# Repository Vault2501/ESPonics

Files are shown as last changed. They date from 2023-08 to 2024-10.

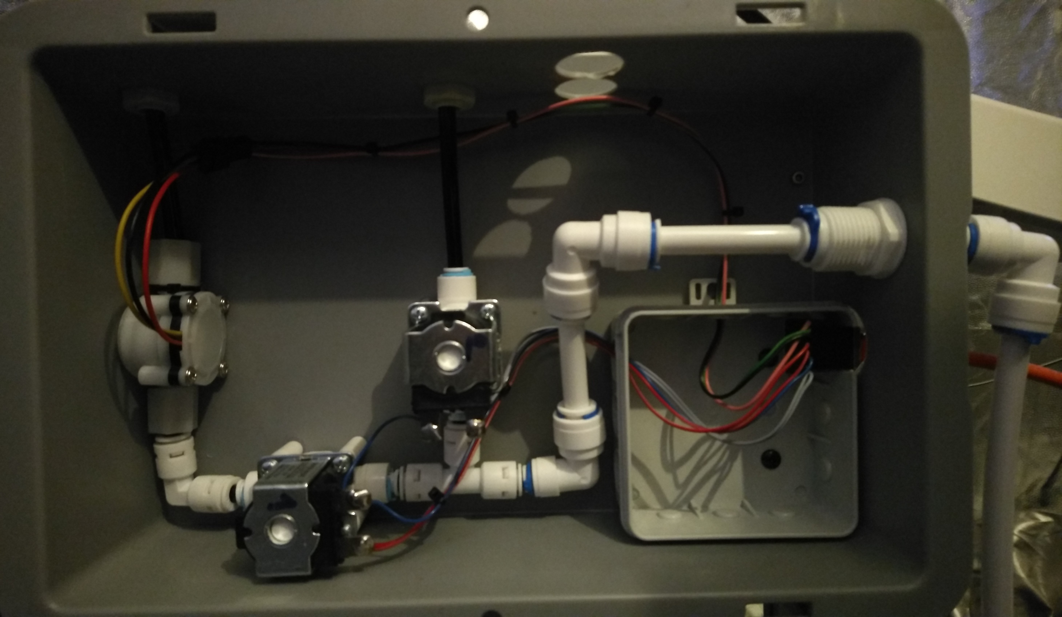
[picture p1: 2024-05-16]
media/20240514_195604_001.jpg

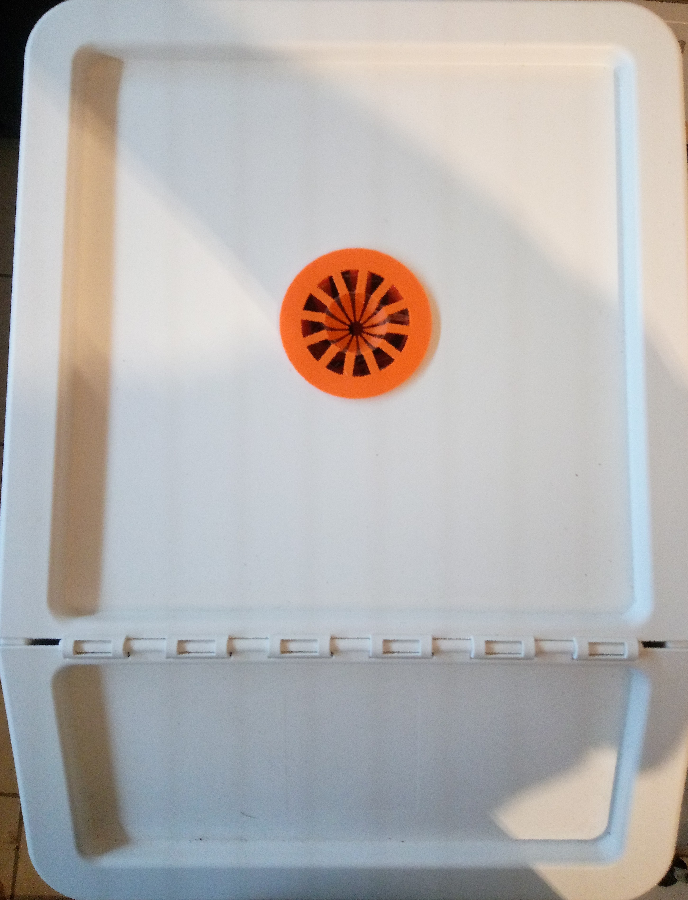
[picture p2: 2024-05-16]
media/IMG_20240429_215926_520.jpg

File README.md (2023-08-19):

# ESPonics
ESPonics is a ESP32 based automated Aeroponics system. It consists of fan, light and pump control as well as sensors for temperature, humidity, water level, ph and ec and is controlled via a web interface.

# Status
This is still WIP

Done:
* Pump control
* Fan Control
* Light Control
* Test Web UI

Current WIP:
* Sensors
* Case models

Todo:
* Userfriendly UI
* Parameter configuration
* Automatic control
* PCB

# Documentation
Documentation will go to the documentaiton folder

# Media
Photos and Videos of this project can be found here:
* Grow and feeding container with pumps: https://pixel.tchncs.de/i/web/post/594626511061922875
* WIP main controller,sensor and light/fan modules: https://pixel.tchncs.de/i/web/post/594629490395300993
* Finished prototype modules: https://pixel.tchncs.de/i/web/post/597583425622062798
* Video testing the pumps: https://makertube.net/w/gAhuFigTPs9yXAJNz8wZ4G

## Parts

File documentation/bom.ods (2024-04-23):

ID
 | Root and Water Container
 | Part | Amount | Source | Price | Comment
2 | IKEA SORTERA 37L | 2 | https://www.ikea.com/de/de/p/sortera-abfalleimer-mit-deckel-weiss-10255897/ | 14.99€
3 | Injectors and hose | 1 | https://www.amazon.de/Yosoo-Drip-Bew%C3%A4sserungskit-K%C3%BChlsystem-Schlauch-Sprinkter-Garten-Terrasse/dp/B072VDN3VG (https://www.amazon.de/Yosoo-Drip-Bewässerungskit-Kühlsystem-Schlauch-Sprinkter-Garten-Terrasse/dp/B072VDN3VG) | 5.26
14 | Plant basket | 1
 | Controller and Modules
 | Part | Amount | Source | Price | Comment
 | Pumps and Valves
 | Part | Amount | Source | Price | Comment
5 | 12V diaphragm pump | 2 | https://www.amazon.de/-/en/gp/product/B01MTNBHPT | 25.99 | Needs adapter for quick connect piping, find better one
1 | Pipe and connectors | 1 | https://www.amazon.de/-/en/gp/product/B099J9TKBH | 15.99
4 | Flow sensor | 1 | https://www.amazon.de/DollaTek-Wasserdurchfluss-Schalter-Durchflussmesser-Z%C3%A4hler-Wei%C3%9F/dp/B07DJ55PPX | 7.99
6 | Solenoid valve | 2 | https://www.amazon.de/Wasserventil-Kunststoff-Elektromagnetventil-Schnellkupplung-Normalerweise/dp/B07Q8KP71J/ | 10.99
 | Light and Fans
 | Part | Amount | Source | Price | Comment
12 | Climate fan | 1
13 | Water cooling fan | 1
15 | LED Light | 1
 | Sensors
 | Part | Amount | Source | Price | Comment
11 | Humidty/Temp | 1 | https://www.amazon.de/-/en/gp/product/B00L3I91TO | 9.49
7 | Temperature | 1 | https://amazon.de/AZDelivery-digitaler-Temperatursensor-Temperaturfühler-wasserdicht/dp/B01MZG48OE | 6.99
8 | TDS | 1 | https://amazon.de/CQRobot-Ocean-Compatible-Scientific-Laboratory/dp/B08KXRHK7H | 11.99
9 | Level | 1 | https://www.amazon.de/Ber%C3%BChrungsloser-Fl%C3%BCssigkeitsstandsensor-Kapazitiver-Wasserstandsschalter-Fl%C3%BCssigkeitserkennungssensor/dp/B0C1BKQ6FH/ (https://www.amazon.de/Berührungsloser-Flüssigkeitsstandsensor-Kapazitiver-Wasserstandsschalter-Flüssigkeitserkennungssensor/dp/B0C1BKQ6FH/) | 6.99
10 | pH | 1 | https://www.amazon.de/Dupla-80290-pH-Elektroden-Set/dp/B002TD8DXM/ | 133.08

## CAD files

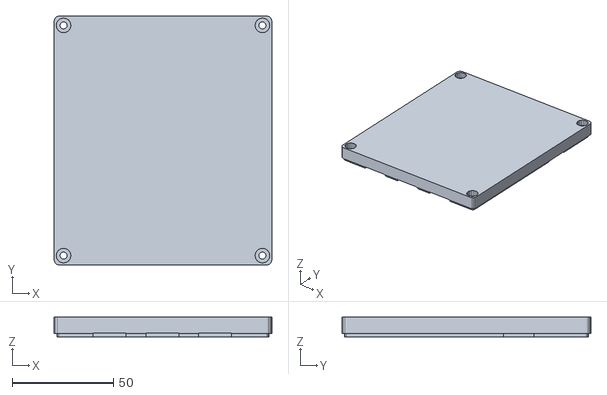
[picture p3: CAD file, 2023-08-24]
3D-models/cases/main_controller/main_controller-top.stl
107.7 x 123.2 x 9.70

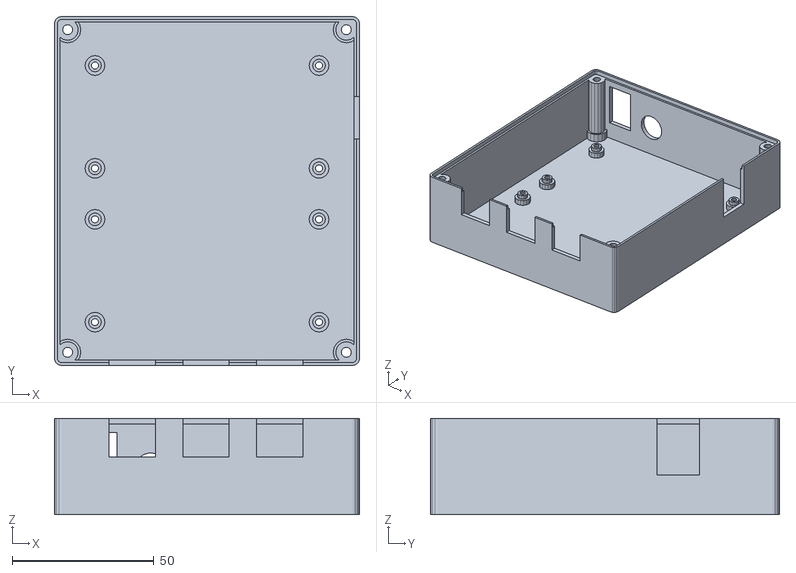
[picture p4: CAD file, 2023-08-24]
3D-models/cases/main_controller/main_controller-bottom.stl
107.7 x 123.2 x 34.0

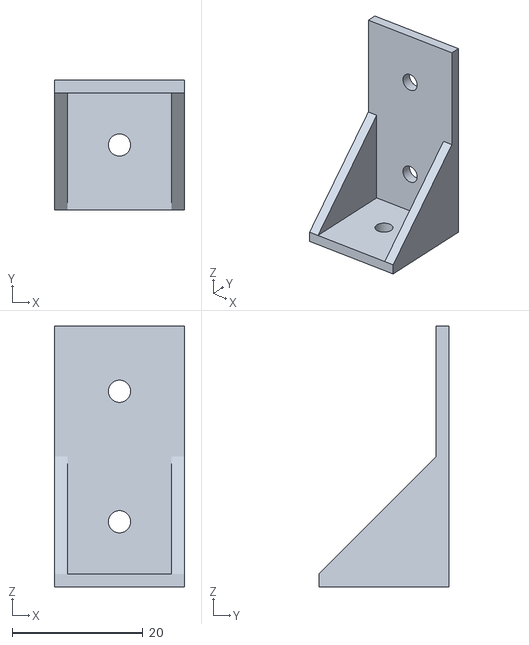
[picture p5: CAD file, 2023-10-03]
3D-models/cases/bar_connector/bar_connector.stl
20.0 x 20.0 x 40.0

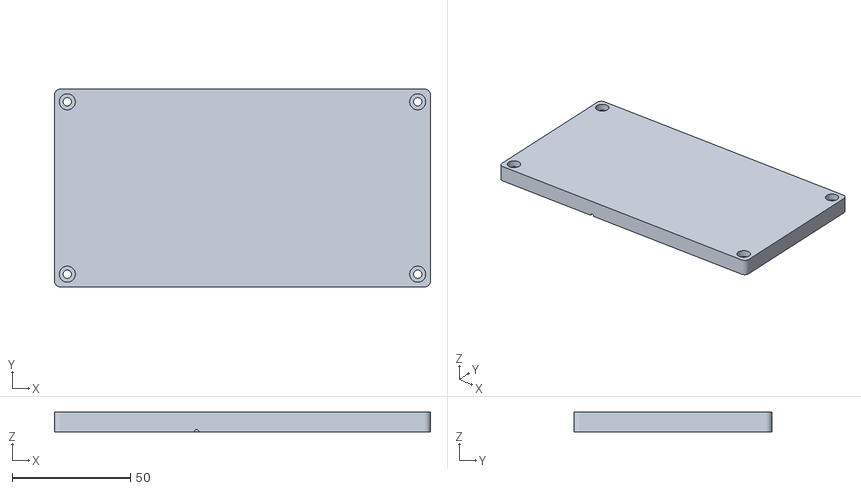
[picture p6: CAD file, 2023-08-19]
3D-models/cases/module_fan_light/module_fan_light-top.stl
158.8 x 83.6 x 8.40

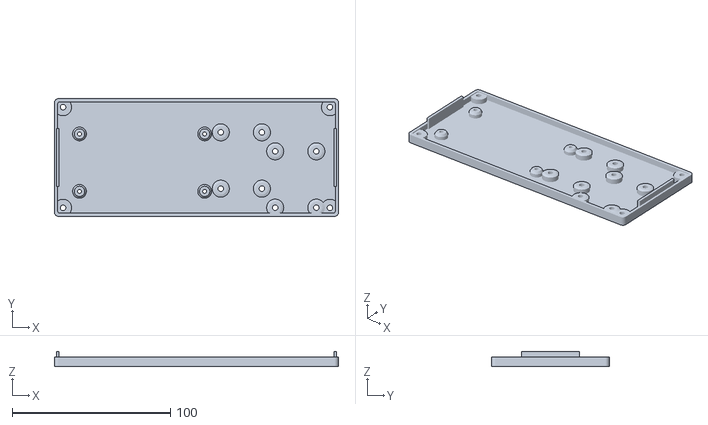
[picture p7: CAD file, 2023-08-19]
3D-models/cases/module_sensor/module_sensor-bottom.stl
179.5 x 74.4 x 9.70

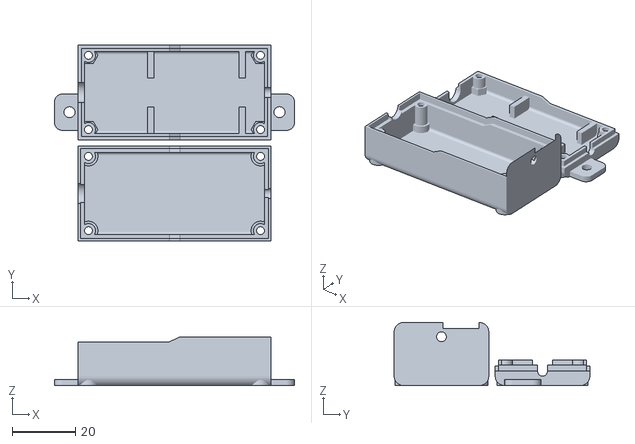
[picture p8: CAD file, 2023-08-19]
3D-models/cases/sensor_connection/sensor_connection-level-all.stl
76.0 x 62.0 x 20.0

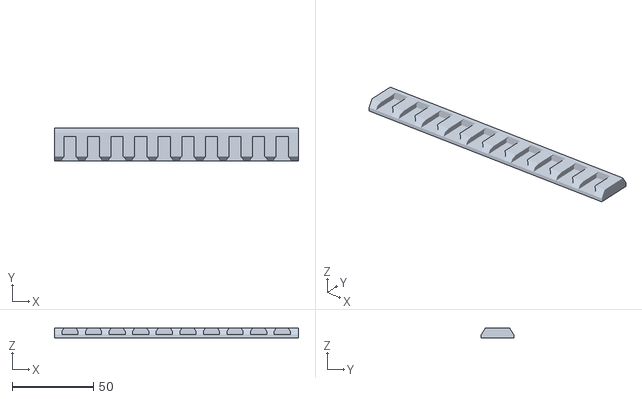
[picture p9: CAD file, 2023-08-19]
3D-models/clip_bar/clip_bar-bar_150mm.stl
150.0 x 20.0 x 6.00

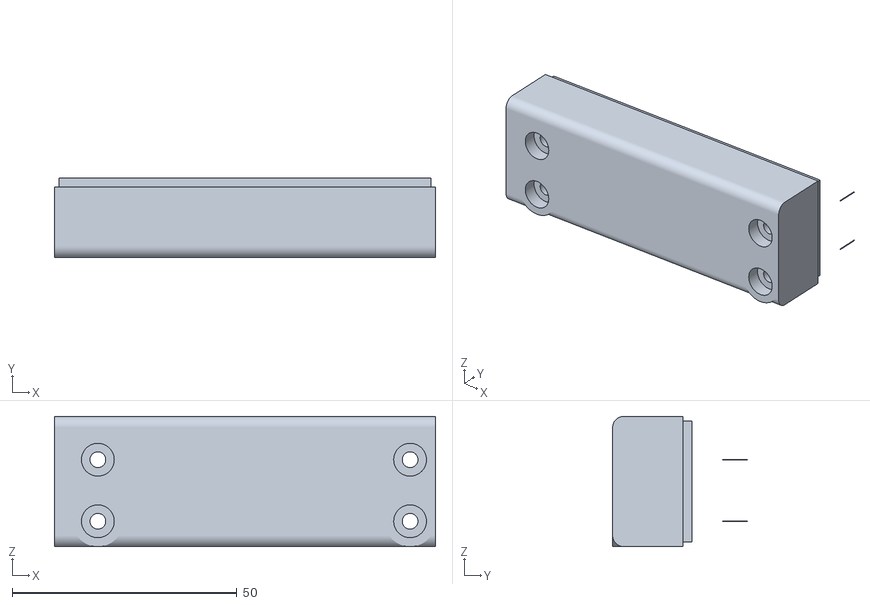
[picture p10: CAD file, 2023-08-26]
3D-models/fan_adapter/fan_adapter-cover-80mm_100mm.stl
84.8 x 30.0 x 29.0

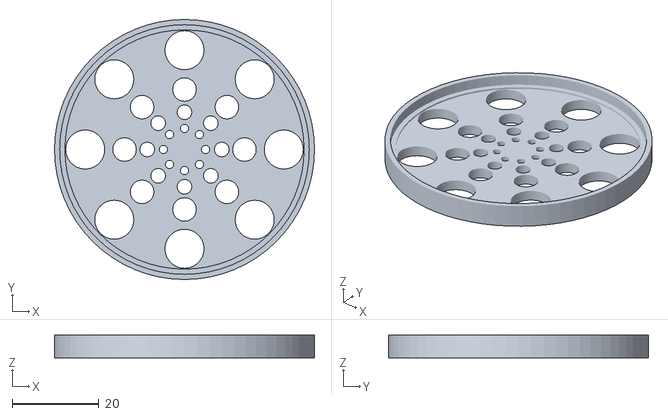
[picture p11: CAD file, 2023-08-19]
3D-models/filter/filter-bottom.stl
60.0 x 60.0 x 5.20

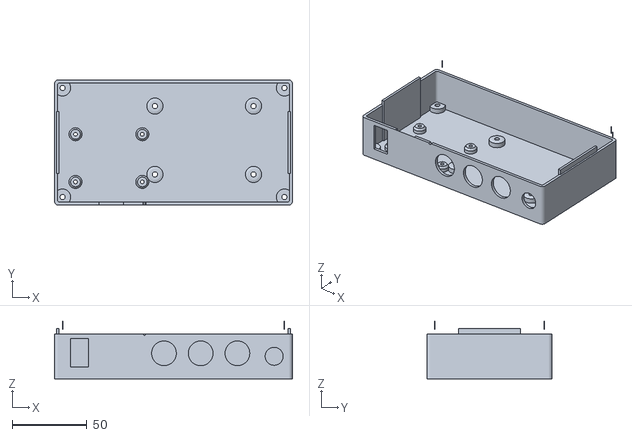
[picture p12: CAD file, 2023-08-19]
3D-models/cases/module_fan_light/module_fan_light-bottom.stl
158.8 x 83.6 x 38.4

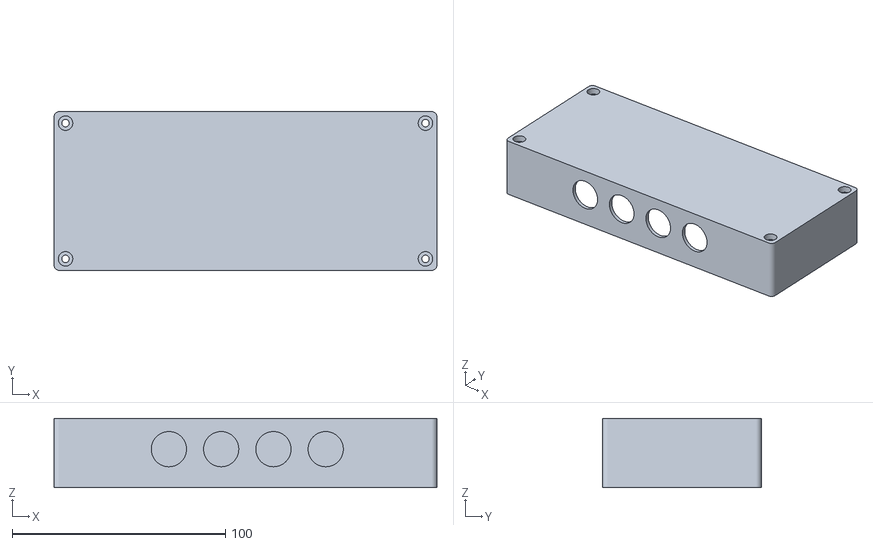
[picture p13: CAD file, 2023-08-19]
3D-models/cases/module_sensor/module_sensor-top.stl
179.5 x 74.4 x 32.4

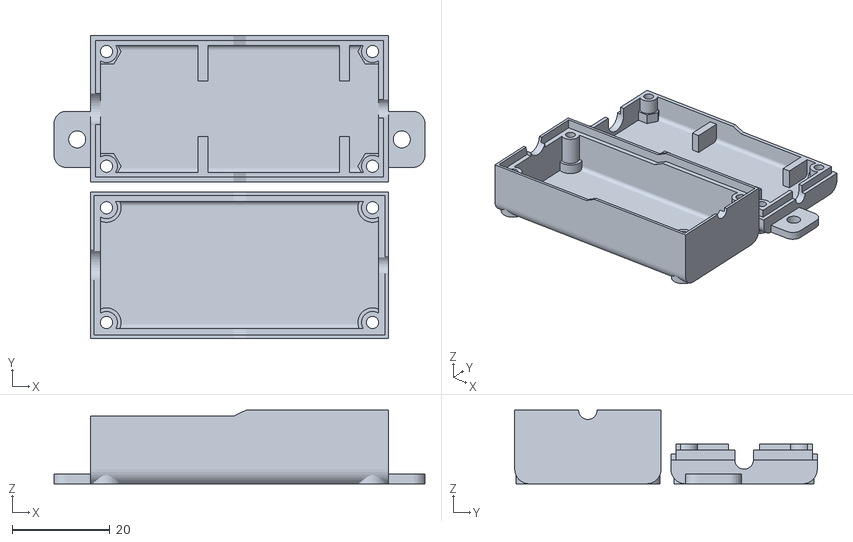
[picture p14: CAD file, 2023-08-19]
3D-models/cases/sensor_connection/sensor_connection-temperature-ec_temp-all.stl
76.0 x 62.0 x 15.1

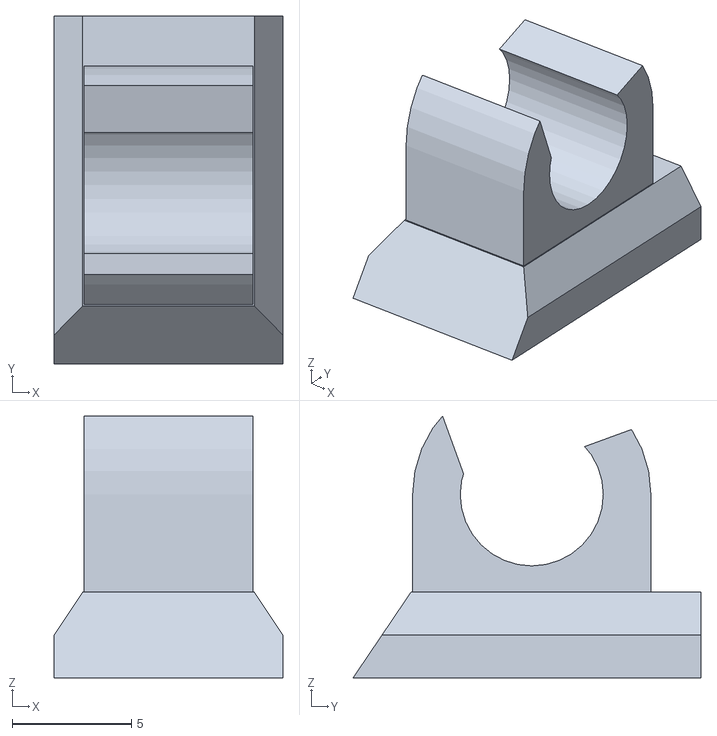
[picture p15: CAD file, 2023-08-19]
3D-models/clip_bar/clip_bar-clip.stl
9.60 x 14.6 x 11.0

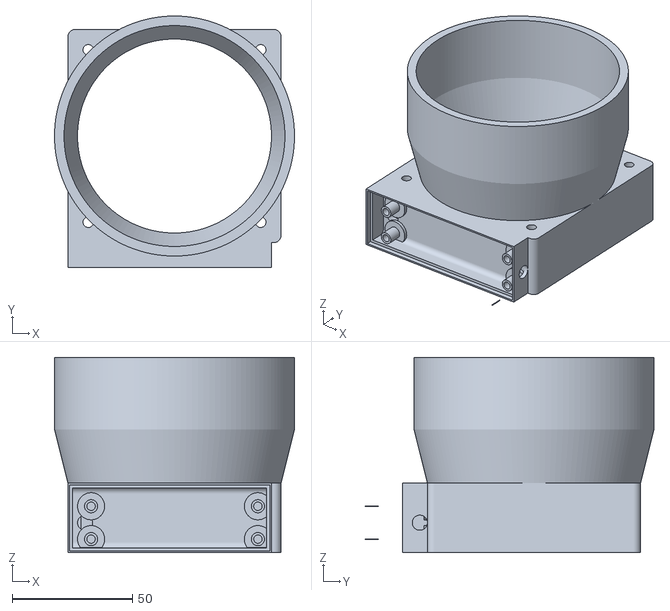
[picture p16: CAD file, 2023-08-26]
3D-models/fan_adapter/fan_adapter-80mm_100mm.stl
100.0 x 120.4 x 81.4

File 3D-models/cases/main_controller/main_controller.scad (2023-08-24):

use <openscad-libraries/case.scad>


// wall thickness
wall                    = 2;
// gap for fitting
gap                     = 0.3;
// height of the lid
height_top              = 8;
// set to true to render the boards
show_boards             = false;
// Which object to render. Choices: top, bottom
object                  = "top";
// render boards (for debugging)
render_boards           = false;

// length of the case screws - determines case height
length_screw_case       = 35;
// diameter of the case screw holes
dia_screw_case          = 3.2+gap;
// length of the board screws
length_screw_board     = 8;
// diameter of screws for boards
dia_screw_board         = 2.2+gap;

// dimensions of boards
dim_boards             = [89.1,52.3,1.6];
// offset of boards in y direction
off_y_boards           = -2;
// x/y offset from the corner for screw holes of the boards
off_xy_screw_boards    = [5,8];

// x/z offset of the ethernet port
off_xz_port_ether       = [10,14];
// dist between ethernet ports
dist_port_ether         = 9.75;
// x/z dimension of the ethernet port
dim_port_ether          = [16+gap,wall+gap,13.5+gap];
// dimension of power switch
dim_switch_power        = [12,wall+gap,19];
// dimeter of power plug
dia_port_power         = 11.8;
// xz offset of power plug and switch
off_xz_power            = [10,10];
// usb port dimension
dim_port_usb            = [wall+gap,15,20];
// xz offset of usb
off_yz_usb              = [80,14];

height_inside = length_screw_case-2*(gap+wall)+2*dia_screw_case;
length_inside = dim_boards[0];
width_inside  = dim_boards[1]+dim_boards[1]+wall+off_y_boards;

width_outside = width_inside+2*(2*dia_screw_case+wall+gap);
length_outside = length_inside+2*(2*dia_screw_case+wall+gap);

off_boards_xy = 2*dia_screw_case+wall+gap;
off_boards_z  = length_screw_board-dim_boards[2];

off_y_power   = width_outside-wall-gap;

echo(off_boards_xy);

if(render_boards)
{
    place_board_1() cube(dim_boards);
    place_board_2() cube(dim_boards);
}

difference()
{
    case(wall=wall,
         gap=gap,
         dia_screws=dia_screw_case,
         render=object,
         height_top=height_top,
         dim_inside=[length_inside,width_inside,height_inside]);
    ethernet_cutout();
    place_board_1(){
        board_screws_cutout();
    }
    place_board_2(){
        board_screws_cutout();
    }
    power_connection();
    usb_cutout();
}

if(object=="bottom" || object == "all")
{
    place_board_1(){
        difference()
        {
            board_screws_addon();
            #board_screws_cutout();
        }
    }

    place_board_2(){
        difference()
        {
            board_screws_addon();
            #board_screws_cutout();
        }
    }
}

module place_board_1()
{
    translate([off_boards_xy,off_boards_xy+off_y_boards,off_boards_z])
    {
        children();
    }
}

module place_board_2()
{
    translate([off_boards_xy,off_boards_xy+off_y_boards+dim_boards[1]+wall,off_boards_z])
    {
        children();
    }
}

module board_screws_cutout()
{
    place_screws(dim_boards[0],
                 dim_boards[1],
                 off_xy_screw_boards[0],
                 off_xy_screw_boards[1])
    {
        translate([0,0,-off_boards_z])
        {
            cylinder(d=dia_screw_board,h=length_screw_board-dim_boards[2]);
            cylinder(d=2*(dia_screw_board+gap),h=dia_screw_board+gap,$fn=6);
        }
    }
}

module board_screws_addon()
{
    place_screws(dim_boards[0],
                 dim_boards[1],
                 off_xy_screw_boards[0],
                 off_xy_screw_boards[1])
    {
        translate([0,0,-off_boards_z])
        {
            cylinder(d=dia_screw_board+wall,h=length_screw_board-dim_boards[2]);
            cylinder(d=2*(dia_screw_board)+wall,h=dia_screw_board+wall);
        }
    }
}

module ethernet_cutout()
{
    translate([off_boards_xy+off_xz_port_ether[0],
               0,
               off_boards_z+off_xz_port_ether[1]])
    {
        for(i=[0:dim_port_ether[0]+dist_port_ether:2*(dim_port_ether[0]+dist_port_ether)])
        {
            translate([i,0,0])
            {
                cube(dim_port_ether);
            }
        }
    }
}

module usb_cutout()
{
    translate([length_outside-wall-gap,off_yz_usb[0],off_yz_usb[1]])
    {
        #cube(dim_port_usb);
    }
}

module power_connection()
{
    translate([off_xz_power[0],off_y_power,off_xz_power[1]])
    {
        cube(dim_switch_power);
        translate([dim_switch_power[0]+12,0,dia_port_power/2])
        {
            rotate([270,0,0])
            {
                cylinder(d=dia_port_power,h=wall+gap);
            }
        }
    }
}

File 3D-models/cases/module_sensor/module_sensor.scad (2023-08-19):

$fn=512;

// generic

// wall thickness
wall                    = 2;
// gap for fitting
gap                     = 0.3;
// height of the bottom part
height_bottom           = 6;
// set to true to render the boards
show_boards             = false;
// Which object to render. Choices: top, bottom
object                  = "top";

// case - most values are calculated

// length of the case screws - determines case height
length_screw_case       = 35;
// diameter of the case screw holes
dia_screw_case          = 3.2+gap;
// diameter of the head for the case screw holes
dia_screw_head_case     = 6.5+gap;
// additional space for the case in the y direction
extra_y_case            = 12;

// generic board values

// length of the board screws - determines the 
length_screw_boards     = 7.5;

// board 1 values and ports

// dimensions of board 1
dim_board_1             = [89.1,52.3,1.6];
// diameter of screws for board 1
dia_screw_board_1       = 2.2+gap;
// diameter of screw heads for board 1
dia_screw_head_board_1  = 4.4+gap;
// offset of board 1 in y direction
off_y_board_1           = 5.5;
// x/y offset from the corner for screw holes of board 1
off_xy_screw_board_1    = [5,8];
// x/z offset of the ethernet port in board 1
off_xz_port_ether       = [8.5,13];
// x/z dimension of the ethernet port
dim_port_ether          = [16+gap,wall,13.5+gap];

// board 2 values and ports

// dimensions of board 2
dim_board_2             = [32.4,42,1.6];
// diameter of screws for board 2
dia_screw_board_2       = 3.2+gap;
// diameter of screw heads for board 2
dia_screw_head_board_2  = 6.5+gap;
// offset of board 2 in y direction
off_y_board_2           = 12;
// x/y offset from the corner for screw holes of board 2
off_xy_screw_board_2    = [3.2,3.2];

// board 3 values and ports

// dimensions of board 3
dim_board_3             = [32.4,42,1.6];
// diameter of screws for board 3
dia_screw_board_3       = 3.2+gap;
// diameter of screw heads for board 3
dia_screw_head_board_3  = 6.5+gap;
// offset of board 3 in y direction
off_y_board_3           = 0;
// x/y offset from the corner for screw holes of board 3
off_xy_screw_board_3    = [3.2,3.2];
// x/z offset of the bnc port in board 3
off_xz_port_bnc         = [8,3.4];
// diameter of the bnc socket
dia_port_bnc            = 14+gap;

// board independent ports

// diameter of the GX16 sockets
dia_port_GX16          = 16.2+gap;
// height for plugs
off_z_plugs            = 24;
// number of GX16 sockets
count_GX16             = 4;
// space between GX16 sockets
spacing_GX16           = 8;


// calculated values
off_x_plugs = dia_screw_head_case+2*wall+dia_port_GX16/2+dim_port_ether[0]+spacing_GX16+off_xz_port_ether[0]+2;

dim_case    = [2*(dia_screw_head_case+2*wall)+dim_board_1[0]+wall+dim_board_2[0]+wall+dim_board_3[0],
               wall+gap+gap+wall+extra_y_case+max((off_y_board_2+dim_board_2[1]),
                                                  (off_y_board_3+dim_board_3[1]),
                                                  (off_y_board_1+dim_board_1[1])),
               length_screw_case+dia_screw_head_case/2];
               
height_top  = dim_case[2]-height_bottom;
//height_front = off_z_plugs+dia_port_GX16/2;
height_base_boards = length_screw_boards - wall - dim_board_1[2];

// main object
if (object == "top")
{
    case_top();
}
if (object == "bottom")
{
    case_bottom();
}


// modules

// top empty case
module case_top()
{
    difference()
    {
        case();
        #cube([dim_case[0],dim_case[1],height_bottom]);
        //#cube([dim_case[0],20,height_front]);
        connector(0);
    }
}

// bottom empty case
module case_bottom()
{
    difference()
    {
        case();
        translate([0,0,height_bottom])
        {
            cube([dim_case[0],dim_case[1],height_top]);
        }
    }
    connector(gap);
}

// complete case
module case()
{
    difference()
    {
        case_pos();
        case_neg();
    }
}

// items to add to the case
module case_pos()
{

    
    difference()
    {
        cube_round(dim_case,5);
        translate([wall,wall,wall])
        {
            cube_round([dim_case[0]-2*wall,
                        dim_case[1]-2*wall,
                        dim_case[2]-2*wall],3);
        }
    }
    
    screws(dia_screw_case,
           dia_screw_head_case,
           length_screw_case,
           [wall+dia_screw_head_case/2,wall+dia_screw_head_case/2],
           [dim_case[0],dim_case[1],dim_case[2]-dia_screw_head_case/2],
           wall,
           mode="shell_bottom");
    
    screws(dia_screw_case,
           dia_screw_head_case,
           length_screw_case,
           [wall+dia_screw_head_case/2,wall+dia_screw_head_case/2],
           [dim_case[0],dim_case[1],dim_case[2]-dia_screw_head_case/2],
           wall,
           mode="shell_top");
    
    place_board_1()
    {
        screws(dia_screw_board_1,
               dia_screw_head_board_1,
               length_screw_boards,
               off_xy_screw_board_1,
               dim_board_1,
               wall,
               mode="shell_bottom");
        
        if(show_boards == true)
        {
            cube_round(dim_board_1,5);
        }
        #port_ether(mode="block");
    }
    place_board_3()
    {
        screws(dia_screw_board_3,
               dia_screw_head_board_3,
               length_screw_boards,
               off_xy_screw_board_3,
               dim_board_3,
               wall,
               mode="shell_bottom");
        
        if(show_boards == true)
        {
            cube_round(dim_board_3,0.2);
        }
    }
    place_board_2()
    {
        screws(dia_screw_board_2,
               dia_screw_head_board_2,
               length_screw_boards,
               off_xy_screw_board_2,
               dim_board_2,
               wall,
               mode="shell_bottom");
        
        if(show_boards == true)
        {
            cube(dim_board_2,5);
        }
    }
}

// elements to be cut out of the case
module case_neg()
{
    screws(dia_screw_case,
           dia_screw_head_case,
           length_screw_case,
           [wall+dia_screw_head_case/2,wall+dia_screw_head_case/2],
           [dim_case[0],dim_case[1],dim_case[2]-dia_screw_head_case/2],
           wall,
           mode="cutout");
    
    port_plugs(dia=dia_port_GX16,
                off_x=off_x_plugs,
                off_z=off_z_plugs,
                spacing=spacing_GX16,
                count=count_GX16,
                wall=wall);
    
    place_board_1()
    {
        screws(dia_screw_board_1,
               dia_screw_head_board_1,
               length_screw_boards,
               off_xy_screw_board_1,
               dim_board_1,
               wall,
               mode="cutout");
        port_ether(mode="cutout");
    }
    place_board_3()
    {
        screws(dia_screw_board_3,
               dia_screw_head_board_3,
               length_screw_boards,
               off_xy_screw_board_3,
               dim_board_3,
               wall,
               mode="cutout");
        port_board_3();
    }
    place_board_2()
    {
        screws(dia_screw_board_2,
               dia_screw_head_board_2,
               length_screw_boards,
               off_xy_screw_board_2,
               dim_board_2,
               wall,
               mode="cutout");
    }
}

// place modules
module place_board_1() 
{
    translate([dia_screw_head_case+2*wall,
               wall+gap+off_y_board_1,
               wall+height_base_boards])
    {
        children();
    }
}

module place_board_2() 
{
    translate([dia_screw_head_case+2*wall+dim_board_1[0]+wall,
               wall+gap+off_y_board_2,
               wall+height_base_boards])
    {
        children();
    }
}

module place_board_3() 
{
    translate([dia_screw_head_case+2*wall+dim_board_1[0]+wall+dim_board_2[0]+wall,
               wall+gap+off_y_board_3,
               wall+height_base_boards])
    {
        children();
    }
}

// port cutouts
module port_ether(mode)
{
    if(mode == "cutout")
    {
        translate([off_xz_port_ether[0],
                   -off_y_board_1-gap-wall,
                   off_xz_port_ether[1]])
        {
            cube(dim_port_ether);
        }
    }
    if(mode == "block")
    {
        translate([off_xz_port_ether[0],
                   -off_y_board_1-gap,
                   off_xz_port_ether[1]+dim_port_ether[2]])
        {
            cube([dim_port_ether[0],5,dim_case[2]-2*wall-height_base_boards-(off_xz_port_ether[1]+dim_port_ether[2])]);
        }
    }
} 

module port_board_3()
{
    translate([off_xz_port_bnc[0] + dia_port_bnc/2,
               -off_y_board_3-wall-gap,
               off_xz_port_bnc[1] + dia_port_bnc/2])
    {
        rotate([270,0,0])
        {
            cylinder(d=dia_port_bnc,h=wall);
        }
    }
}
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

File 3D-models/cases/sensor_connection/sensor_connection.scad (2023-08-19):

$fn=32;

render = "all";
ventilation = false;
connector = true;
wall = 2;
gap = 0.3;

len_board = 27;
wid_board = 26;

height_case = 20;

dia_GX16 = 6.3;
dia_sensor = 3.1;
dia_screw = 2.2+gap;

dia_screw_connector = 3.2+gap;

extra_GX16 = 20;
extra_sensor = 10;


len_case = len_board + extra_GX16 + extra_sensor + 2*wall;
wid_case = wid_board + 2*wall;

height_bottom_GX16=1.5*wall+dia_GX16/2;
height_bottom_sensor=1.5*wall+dia_sensor/2;


// render object
if(render == "bottom" || render == "all")
{
    bottom();
}

if( render == "top" || render == "all")
{
    translate([0,-wall,max(height_bottom_GX16,height_bottom_sensor)
                  +height_case
                  -max(height_bottom_GX16,height_bottom_sensor)])
    {
        rotate([180,0,0])
        {
            top();
        }
    }
}


// modules
module top()
{   
    difference()
    {
        case();
        case_cut_bottom(gap=gap);
    }
}
 
module bottom()
{   
    difference()
    {
        case();
        case_cut_top();
    }
    board_frame();
}

module case_cut_bottom(gap=0)
{
    if(connector==true)
    {
        connector();
    }
    // GX side
    cube([len_case/2-(abs(height_bottom_GX16-height_bottom_sensor)),
          wid_case,
          height_bottom_GX16]);
    
    difference()
    {
        translate([wall/2-gap,wall/2-gap,0])
        {
            cube([len_case/2-(abs(height_bottom_GX16-height_bottom_sensor))-wall/2+gap,
                  wid_case-wall+2*gap,
                  height_bottom_GX16+wall+gap]);
        }
        translate([wall/2-gap,wid_case/2-dia_GX16/2+gap,height_bottom_GX16])
        {
            cube([len_case/2-(abs(height_bottom_GX16-height_bottom_sensor)),
                 dia_GX16-2*gap,
                 wall+gap]);
        }
    }
    
    // transition
    hull ()
    {
        translate([len_case/2-(abs(height_bottom_GX16-height_bottom_sensor))-0.1,0,0])
        {
            cube([0.1,wid_case,height_bottom_GX16]);
            translate([2*(abs(height_bottom_GX16-height_bottom_sensor))+0.1,0,0])
            {
                cube([0.1,wid_case,height_bottom_sensor]);
            }
        }
    }
    hull ()
    {
        translate([len_case/2-(abs(height_bottom_GX16-height_bottom_sensor))-0.1,wall/2-gap,wall+gap])
        {
            cube([0.1,wid_case-wall+2*gap,height_bottom_GX16]);
            translate([2*(abs(height_bottom_GX16-height_bottom_sensor))+0.1,0,0])
            {
                cube([0.1,wid_case-wall+2*gap,height_bottom_sensor]);
            }
        }
    }
    
    
    // sensor side
    translate([len_case/2+(abs(height_bottom_GX16-height_bottom_sensor)),0,0])
    {
        cube([len_case/2-(abs(height_bottom_GX16-height_bottom_sensor)),
              wid_case,
              height_bottom_sensor]);
        difference()
        {
            translate([0,wall/2-gap,wall])
            {
                cube([len_case/2-(abs(height_bottom_GX16-height_bottom_sensor-wall/2))-wall+gap,
                      wid_case-wall+2*gap,
                      height_bottom_sensor+gap]);
            }
            translate([0,wid_case/2-dia_sensor/2+gap,height_bottom_sensor])
            {
                cube([len_case/2-(abs(height_bottom_GX16-height_bottom_sensor-wall/2))-wall+gap,
                      dia_sensor-2*gap,
                      wall+gap]);
            }
        }
    }
}

module case_cut_top()
{
    difference()
    {
        case_solid(mki=0);
        case_cut_bottom();
    }
}


module case()
{
    difference()
    {
        union()
        {
            case_solid(mki=6);
            if(connector==true)
            {
                connector();
            }
        }
        translate([wall,wall,wall])
        {
            cube_round([len_case-2*wall,
                        wid_case-2*wall,
                        height_case-2*wall],mki=2,plane="yz");
        }
        cutouts();
    }
    difference()
    {
        screw_holes(mode="additive");
        screw_holes(mode="subtractive");
    }
}

module case_solid(mki=4)
{
    cube_round([len_case,wid_case,height_case],mki=mki,plane="yz");
}

module board_frame()
{
    translate([wall+extra_GX16,wall,wall])
    {
        difference()
        {
            #cube([len_board+2*wall,wid_board,height_bottom_sensor]);
            translate([wall,0,0])
            {
                cube([len_board,wid_board,height_bottom_sensor]);
            }
            translate([0,(wid_case-3*dia_sensor)/2-wall,0])
            {
                cube([len_board+2*wall,3*dia_sensor,height_bottom_sensor]);
            }
        }
    }
}

module cutouts()
{
    hole_GX16();
    hole_sensor();
    screw_holes(mode="subtractive");
    if(ventilation==true)
    {
        ventilation_holes();
    }
}

module connector()
{
    len_connector=dia_screw_connector+3*wall;
    wid_connector=dia_screw_connector+4*wall;
    
    loc=[
         [-len_connector+wall,1.5*wall,0],
         [len_case-wall,1.5*wall,0],
        ];
    
    for(i=loc)
    {
        translate(i)
        {
            difference()
            {
                cube_round([len_connector,wid_connector,wall]);
                translate([dia_screw_connector/2+1.5*wall,dia_screw_connector/2+2*wall,0])
                {
                    cylinder(d=dia_screw_connector,h=wall);
                }
            }
        }
    }
}

module screw_holes(mode="additive")
{
    dia_screw_head = 2*dia_screw;
    loc_screws=[
                [wall+dia_screw/2,wall+dia_screw/2,0],
                [wall+dia_screw/2,wid_case-wall-dia_screw/2,0],
                [len_case-wall-dia_screw/2,wall+dia_screw/2,0],
                [len_case-wall-dia_screw/2,wid_case-wall-dia_screw/2,0]
               ];
    
    for(i=loc_screws)
    {
        translate(i)
        {
            if(mode=="subtractive")
            {
                cylinder(d=dia_screw,h=height_case);
                cylinder(d=dia_screw_head,h=dia_screw,$fn=6);
                translate([0,0,height_case-dia_screw])
                {
                    cylinder(d=dia_screw_head,h=dia_screw);
                }
            }
            if(mode=="additive")
            {
                cylinder(d=dia_screw+wall,h=height_case);
                cylinder(d=dia_screw_head+wall/2,h=dia_screw+wall,$fn=6);
                translate([0,0,height_case-dia_screw-wall])
                {
                    cylinder(d=dia_screw_head+wall/2,h=dia_screw+wall);
                }
            }
        }
    }
}

module hole_GX16()
{
    translate([0,wid_case/2,dia_GX16/2+1.5*wall])
    {
        rotate([0,90,0])
        {
            cylinder(h=wall,d=dia_GX16);
        }
    }
}

module hole_sensor()
{
    translate([len_case-wall,wid_case/2,dia_sensor/2+1.5*wall])
    {    
        rotate([0,90,0])
        {
            cylinder(h=wall,d=dia_sensor);
        }
    }
}


module ventilation_holes()
{
    intersection()
    {
        for(i=[2*wall : 2*wall : ((len_case-2*wall)/2*wall)])
        {
            translate([i,wall,height_case-wall])
            {
                cube([wall,wid_case-2*wall,wall]);
            }
        }
        for(i=[2*wall : 2*wall : ((wid_case-2*wall)/2*wall)])
        {
            translate([wall,i,height_case-wall])
            {
                cube([len_case-2*wall,wall,wall]);
            }
        }
    }
}

module cube_round(dim,mki=5,plane="xy"){
    if(mki<=0)
    {
        cube(dim);
    }
    else
    {
        if(plane=="xy")
        {
            translate([mki/2,mki/2,0])
            {
                linear_extrude(dim[2])
                {
                    minkowski()
                    {
                        square([dim[0]-mki,dim[1]-mki]);
                        circle(d=mki);
                    }
                }
            }
        }
        if(plane=="yz")
        {
            translate([0,mki/2,dim[2]-mki/2])
            {
                rotate([0,90,0])
                {
                    linear_extrude(dim[0])
                    {
                        minkowski()
                        {
                            square([dim[2]-mki,dim[1]-mki]);
                            circle(d=mki);
                        }
                    }
                }
            }
        }
        if(plane=="xz")
        {
            translate([mki/2,dim[1],mki/2])
            {
                rotate([90,0,0])
                {
                    linear_extrude(dim[1])
                    {
                        minkowski()
                        {
                            square([dim[0]-mki,dim[2]-mki]);
                            circle(d=mki);
                        }
                    }
                }
            }
        }
    }
}

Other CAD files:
3D-models/filter/filter_clip.stl
3D-models/cases/sensor_connection/sensor_connection-humidity_all.stl
3D-models/clip_bar/clip_bar-bar_77mm.stl
3D-models/fan_adapter/fan_adapter-cover.stl
3D-models/clip_bar/clip_bar.scad
3D-models/cases/bar_connector/bar_connector.scad
3D-models/cases/module_fan_light/module_fan_light.scad
3D-models/clip_bar/clip_bar-bar_180mm.stl
3D-models/fan_adapter/fan_adapter-110mm.stl
3D-models/fan_adapter/fan_adapter.scad
3D-models/filter/filter-top.stl
3D-models/filter/filter.scad

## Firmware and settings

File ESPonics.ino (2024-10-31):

#include <WiFiManager.h>
#define WEBSERVER_H
#include <ESPAsyncWebServer.h>
#include <Wire.h>
#include <TaskScheduler.h>
#include <UnitecRCSwitch.h>
#include <DHT.h>
#include <OneWire.h>
#include <DallasTemperature.h>
#include <ArduinoJson.h>
#include <Preferences.h>
#include <ArduinoOTA.h>
#include "time.h"
#include "index.h"
#include "struct.h"
#include "vars.h"
#include "wifimanager.h"
#include "ph2.h"
#include "tds.h"
#include "config.h"
#include "sensors.h"
#include "helper.h"

Preferences preferences;

AsyncWebServer server(8080);
AsyncWebSocket ws("/ws");

DHT dht(DHT_PIN, DHTTYPE);

PH ph(&message.log);
TDS tds;

OneWire oneWire(TEMP_PIN);
DallasTemperature temp_sensor(&oneWire);

Scheduler ts;
void enableSpray();
void disableSpray();
void enableLight();
void disableLight();
void openValve1();
Task tPump(schedule.spray_period *TASK_MILLISECOND, TASK_FOREVER, &enableSpray, &ts, true);
Task tPumpOff(schedule.spray_duration *TASK_MILLISECOND, TASK_ONCE, &disableSpray, &ts, false);
Task tLightOn(schedule.light_on *TASK_SECOND, TASK_FOREVER, &enableLight, &ts, true);
Task tLightOff(schedule.light_off *TASK_SECOND, TASK_ONCE, &disableLight, &ts, false);
Task tOpenValve1(schedule.valve1_delay *TASK_MILLISECOND, TASK_ONCE, &openValve1, &ts, false);


//////////////////////////////////////////////
// Web part

void notifyClients() {
  ws.textAll("{\n\t\"pump1_state\": \""
             + String(state.pump1) + "\",\
               \n\t\"pump2_state\": \""
             + String(state.pump2) + "\",\
               \n\t\"valve1_state\": \""
             + String(state.valve1) + "\",\
               \n\t\"valve2_state\": \""
             + String(state.valve2) + "\",\
               \n\t\"fan1_state\": \""
             + String(state.fan1) + "\",\
               \n\t\"fan1_speed\": \""
             + String(settings.fan1_speed) + "\",\
               \n\t\"fan2_state\": \""
             + String(state.fan2) + "\",\
               \n\t\"light_state\": \""
             + String(state.light) + "\",\
               \n\t\"light_on\": \""
             + String(schedule.light_on) + "\",\
               \n\t\"light_off\": \""
             + String(schedule.light_off) + "\",\
               \n\t\"scheduler_active\": \""
             + String(settings.scheduler_active) + "\",\
               \n\t\"flow_rate\": \""
             + String(sensors.flow_rate) + "\",\
               \n\t\"flow_quantity\": \""
             + String(sensors.flowMilliLiters) + "\",\
               \n\t\"flow_total\": \""
             + String(sensors.totalMilliLiters) + "\",\
               \n\t\"spray_period\": \""
             + String(schedule.spray_period) + "\",\
               \n\t\"spray_duration\": \""
             + String(schedule.spray_duration) + "\",\
               \n\t\"dhtValueTemp\": \""
             + String(sensors.dhtValueTemp) + "\",\
               \n\t\"dhtValueHumidity\": \""
             + String(sensors.dhtValueHumidity) + "\",\
               \n\t\"dallasValueTemp\": \""
             + String(sensors.dallasValueTemp) + "\",\
               \n\t\"ph_value\": \""
             + String(sensors.ph_value) + "\",\
               \n\t\"ph_calibrated\": \""
             + String(settings.ph_calibrated) + "\",\
               \n\t\"ph_analog\": \""
             + String(sensors.ph_analog) + "\",\
               \n\t\"ph_neutralVoltage\": \""
             + String(settings.ph_neutralVoltage) + "\",\
               \n\t\"ph_acidVoltage\": \""
             + String(settings.ph_acidVoltage) + "\",\
               \n\t\"tds_value\": \""
             + String(sensors.tds_value) + "\",\
               \n\t\"tds_calibrated\": \""
             + String(settings.tds_calibrated) + "\",\
               \n\t\"tds_analog\": \""
             + String(sensors.tds_analog) + "\",\
               \n\t\"water_state\": \""
             + String(state.water) + "\",\
               \n\t\"esp_day\": \""
             + String(message.dayStamp) + "\",\
               \n\t\"esp_time\": \""
             + String(message.timeStamp) + "\",\
               \n\t\"message_log\": \""
             + String(message.log) + "\"\
               \n}");
}

void handleWebSocketMessage(void *arg, uint8_t *data, size_t len) {
  AwsFrameInfo *info = (AwsFrameInfo *)arg;
  if (info->final && info->index == 0 && info->len == len && info->opcode == WS_TEXT) {
    data[len] = 0;
    D_PRINTLN("Data received: ");
    D_PRINTLN((char *)data);

    DynamicJsonDocument garden_command(1024);
    DeserializationError error = deserializeJson(garden_command, data);
    if (error) {
      Serial.println("Deserialisation failed");
      Serial.println(error.f_str());
      return;
    }

    const char *command_type = garden_command["type"];
    D_PRINT("  [handleWebSocketMessage] Command type: ");
    D_PRINTLN(command_type);

    const char *command_item = garden_command["item"];
    D_PRINT("  [handleWebSocketMessage] Command item: ");
    D_PRINTLN(command_item);

    unsigned long int command_value = garden_command["value"];
    D_PRINT("  [handleWebSocketMessage] Command value: ");
    D_PRINTLN(command_value);

    if (strcmp(command_type, "toggle") == 0) {
      if (strcmp(command_item, "pump1") == 0) {
        state.pump1 = !state.pump1;
        settings.scheduler_active = 0;
        notifyClients();
      }
      if (strcmp(command_item, "pump2") == 0) {
        state.pump2 = !state.pump2;
        settings.scheduler_active = 0;
        notifyClients();
      }
      if (strcmp(command_item, "valve1") == 0) {
        state.valve1 = !state.valve1;
        settings.scheduler_active = 0;
        notifyClients();
      }
      if (strcmp(command_item, "valve2") == 0) {
        state.valve2 = !state.valve2;
        settings.scheduler_active = 0;
        notifyClients();
      }
      if (strcmp(command_item, "scheduler") == 0) {
        settings.scheduler_active = !settings.scheduler_active;
        preferences.begin("garden", false);
        preferences.putBool("scheduler", settings.scheduler_active);
        preferences.end();
        notifyClients();
      }
      if (strcmp(command_item, "fan1") == 0) {
        state.fan1 = !state.fan1;
        notifyClients();
      }
      if (strcmp(command_item, "fan2") == 0) {
        state.fan2 = !state.fan2;
        notifyClients();
      }
      if (strcmp(command_item, "light") == 0) {
        D_PRINTLN("  [handleWebSocketMessage] light toggle command");
        light_toggle = 0;
        state.light = !state.light;
        settings.scheduler_active = 0;
        notifyClients();
      }
      if (strcmp(command_item, "calibrate_ph") == 0) {
        ph.calibrate();
        settings.ph_calibrated = ph.getCalibrated();
        if(settings.ph_calibrated)
        {
          settings.ph_acidVoltage = ph.getAcidVoltage();
          settings.ph_neutralVoltage = ph.getNeutralVoltage();
          settings.ph_calibrated = ph.getCalibrated();
          preferences.begin("garden", false);
          preferences.putFloat("ph_neutralVoltage", settings.ph_neutralVoltage);
          preferences.putFloat("ph_acidVoltage", settings.ph_acidVoltage);
          preferences.putBool("ph_calibrated", settings.ph_calibrated);
          preferences.end();       
          notifyClients();
        }
      }
      if (strcmp(command_item, "calibrate_tds") == 0) {
        float tdsc = garden_command["value"];
        tds.calibrate(tdsc);
        settings.tds_calibrated = tds.getCalibrated();
        if(settings.tds_calibrated)
        {
          settings.tds_kvalue = tds.getKvalue();
          preferences.begin("garden", false);
          preferences.putFloat("tds_kvalue", settings.tds_kvalue);
          preferences.putBool("tds_calibrated", settings.tds_calibrated);
          preferences.end();
          notifyClients();
        } 
      }    
      if (strcmp(command_item, "calibrate_flow") == 0) {
        Serial.println("Calibrating flow");
        flow_cal_measured = calibrateFlow();
      }   
    }
    if (strcmp(command_type, "update") == 0) {
      if (strcmp(command_item, "light_on") == 0) {
        schedule.light_on = garden_command["value"];
        preferences.begin("garden", false);
        preferences.putULong("light_on", schedule.light_on);
        preferences.end();
        tLightOn.setInterval(schedule.light_on * TASK_SECOND);
        settings.scheduler_active = 1;
        notifyClients();
      }
      if (strcmp(command_item, "light_off") == 0) {
        schedule.light_off = garden_command["value"];
        preferences.begin("garden", false);
        preferences.putULong("light_off", schedule.light_off);
        preferences.end();
        tLightOn.setInterval(schedule.light_off * TASK_SECOND);
        settings.scheduler_active = 1;
        notifyClients();
      }
      if (strcmp(command_item, "spray_period") == 0) {
        schedule.spray_period = garden_command["value"];
        preferences.begin("garden", false);
        preferences.putULong("spray_period", schedule.spray_period);
        preferences.end();
        tPump.setInterval(schedule.spray_period * TASK_MILLISECOND);
        settings.scheduler_active = 1;
        notifyClients();
      }
      if (strcmp(command_item, "spray_duration") == 0) {
        schedule.spray_duration = garden_command["value"];
        preferences.begin("garden", false);
        preferences.putULong("spray_duration", schedule.spray_duration);
        preferences.end();
        tPumpOff.setInterval(schedule.spray_duration * TASK_MILLISECOND);
        settings.scheduler_active = 1;
        notifyClients();
      }
      if (strcmp(command_item, "flow_amount") == 0) {
        unsigned int temp = garden_command["value"];
        settings.flow_calibration = (temp / flow_cal_measured);
        Serial.print("settings.flow_calibration: ");
        Serial.println(settings.flow_calibration);
        //preferences.begin("garden", false);
        //preferences.putULong("spray_duration", schedule.spray_duration);
        //preferences.end();
        //tPumpOff.setInterval(schedule.spray_duration * TASK_MILLISECOND);
        //settings.scheduler_active = 1;
        //notifyClients();
      }
      if (strcmp(command_item, "fan1_speed") == 0) {
        settings.fan1_speed = garden_command["value"];
        preferences.begin("garden", false);
        preferences.putULong("fan1_speed", settings.fan1_speed);
        preferences.end();
        setFanPwm(FANPWM1_PIN, settings.fan1_speed);
        notifyClients();
      }
    }
  }
}

void onEvent(AsyncWebSocket *server, AsyncWebSocketClient *client, AwsEventType type,
             void *arg, uint8_t *data, size_t len) {
  switch (type) {
    case WS_EVT_CONNECT:
      Serial.printf("WebSocket client #%u connected from %s\n", client->id(), client->remoteIP().toString().c_str());
      break;
    case WS_EVT_DISCONNECT:
      Serial.printf("WebSocket client #%u disconnected\n", client->id());
      break;
    case WS_EVT_DATA:
      handleWebSocketMessage(arg, data, len);
      break;
    case WS_EVT_PONG:
    case WS_EVT_ERROR:
      break;
  }
}

void initWebSocket() {
  ws.onEvent(onEvent);
  server.addHandler(&ws);
}

String processor(const String &var) {
  if (var == "PUMP1_STATE") {
    return String(state.pump1);
  } else if (var == "PUMP2_STATE") {
    return String(state.pump2);
  } else if (var == "VALVE1_STATE") {
    return String(state.valve1);
  } else if (var == "VALVE2_STATE") {
    return String(state.valve2);
  } else if (var == "SCHEDULER_ACTIVE") {
    return String(settings.scheduler_active);
  } else if (var == "FLOW_RATE") {
    return String(sensors.flow_rate);
  } else if (var == "FLOW_QUANTITY") {
    return String(sensors.totalMilliLiters);
  } else if (var == "SPRAY_PERIOD") {
    return String(schedule.spray_period);
  } else if (var == "SPRAY_DURATION") {
    return String(schedule.spray_duration);
  } else if (var == "FAN1_STATE") {
    return String(state.fan1);
  } else if (var == "FAN2_STATE") {
    return String(state.fan2);
  } else if (var == "FAN1_SPEED") {
    return String(settings.fan1_speed);
  } else if (var == "LIGHT_STATE") {
    return String(state.light);
  } else if (var == "LIGHT_ON") {
    return String(schedule.light_on);
  } else if (var == "LIGHT_OFF") {
    return String(schedule.light_off);
  } else if (var == "DHT_TEMP_VALUE") {
    return String(sensors.dhtValueTemp);
  } else if (var == "DHT_HUMIDITY_VALUE") {
    return String(sensors.dhtValueHumidity);
  } else if (var == "DALLAS_TEMP_VALUE") {
    return String(sensors.dallasValueTemp);
  } else if (var == "WATER_STATE") {
    return String(state.water);
  } else if (var == "PH_VALUE") {
    return String(sensors.ph_value);
  } else if (var == "PH_ANALOG") {
    return String(sensors.ph_analog);
  } else if (var == "PH_CALIBRATED") {
    return String(settings.ph_calibrated);
  } else if (var == "TDS_VALUE") {
    return String(sensors.tds_value);
  } else if (var == "TDS_ANALOG") {
    return String(sensors.tds_analog);
  } else if (var == "TDS_CALIBRATED") {
    return String(settings.tds_calibrated);  
  } else {
    D_PRINTLN("template: Unknown variable");
    return String("  [processor] Unknown variable");
  }
}


//////////////////////////////////////////////
/// Pumps


void setPumpState() {
  digitalWrite(PUMP1_PIN, state.pump1);
  digitalWrite(PUMP2_PIN, state.pump2);
}

void enableSpray() {
  D_PRINT("  [enableSpray] Enabling spray ");
  D_PRINTLN(settings.active_pump);
  if (settings.active_pump == 1) {
    state.pump1 = 0;
  }
  if (settings.active_pump == 2) {
    state.pump2 = 0;
  }
  //state.valve1 = 0;
  tOpenValve1.restartDelayed();
  notifyClients();
  tPumpOff.restartDelayed();
}

void disableSpray() {
  D_PRINT("  [disableSpray] Disabling Spray ");
  D_PRINTLN(settings.active_pump);
  if (settings.active_pump == 1) {
    state.pump1 = 1;
  }
  if (settings.active_pump == 2) {
    state.pump2 = 1;
  }
  state.valve1 = 1;
  notifyClients();
}


//////////////////////////////////////////////
/// Valves

void openValve1()
{
  state.valve1=0;
}

void setValveState() {
  digitalWrite(VALVE1_PIN, state.valve1);
  digitalWrite(VALVE2_PIN, state.valve2);
}

//////////////////////////////////////////////
/// Fans

void setFanState() {
  digitalWrite(FAN1_PIN, state.fan1);
  digitalWrite(FAN2_PIN, state.fan2);
}

void setFanPwm(int pin, int duty) {
  D_PRINT("  [setFanPwm] Setting PWM ");
  D_PRINT(pin);
  D_PRINT(" to ");
  D_PRINT(duty);
  int dutyCycle = (duty * 255) / 100;
  D_PRINTLN(dutyCycle);
  ledcWrite(PWM_FANCHANNEL, dutyCycle);
  //analogWrite(pin, (duty / 100) * 1023);
}
//////////////////////////////////////////////
/// Light

UnitecRCSwitch mySwitch;

UnitecRCSwitch::ButtonCodes codes = {
  { 13721648, 14595904, 13946480, 14372784 },  // Button A ON codes
  { 13806992, 13996448, 14506528, 13831184 },  // Button A OFF codes
  { 14372788, 13946484, 14595908, 13721652 },  // Button B ON codes
  { 13831188, 14506532, 13996452, 13806996 },  // Button B OFF codes
  { 14595916, 13721660, 14372796, 13946492 },  // Button C ON codes
  { 13996460, 13807004, 13831196, 14506540 },  // Button C OFF codes
  { 13806994, 13996450, 14506530, 13831186 },  // Button D ON codes
  { 13721650, 14595906, 13946482, 14372786 },  // Button D OFF codes
};

void setLightState() {
  if (light_toggle == 0) {
    if (state.light == 1) {
      // Turn light off
      D_PRINTLN("  [setLightState] Turning light off");
      mySwitch.switchOff(UnitecRCSwitch::SOCKET_A);
    }

    if (state.light == 0) {
      // Turn light on
      D_PRINTLN("  [setLightState] Turning light on");
      mySwitch.switchOn(UnitecRCSwitch::SOCKET_A);
    }
    light_toggle = !light_toggle;
  }
}

void enableLight() {
  D_PRINTLN("  [enableLight] Enabling light");
  state.light = 0;
  light_toggle = 0;
  notifyClients();
  tLightOff.restartDelayed();
};

void disableLight() {
  D_PRINTLN("  [disableLight] Disabling Light ");
  state.light = 1;
  light_toggle = 0;
  notifyClients();
};

//////////////////////////////////////////////
/// Flow Rate

void IRAM_ATTR pulseCounter() {
  pulseCount++;
}

unsigned long calibrateFlow() {
  // get current amount
  unsigned long calibStartMilliLiters = sensors.totalMilliLiters;

  // turn on pump
  state.pump1 = 0;
  state.valve2 = 0;

  // wait 30 sec
  delay(30000);

  // turn off pump
  state.pump1 = 1;
  state.valve2 = 1;

  // calculate measured milliliters
  unsigned long calibMeasurement = sensors.totalMilliLiters - calibStartMilliLiters;
  Serial.print("calibMeasurement: ");
  Serial.println(calibMeasurement);
  // use  user provided amount that really was pumped to calculate calibration factor
  return 2*calibMeasurement;
}

void getFlowRate() {
  currentFlowMillis = millis();
  if (currentFlowMillis - previousFlowMillis > sensors.interval) {

    pulse1Sec = pulseCount;
    pulseCount = 0;

    // Because this loop may not complete in exactly 1 second intervals we calculate
    // the number of milliseconds that have passed since the last execution and use
    // that to scale the output. We also apply the calibrationFactor to scale the output
    // based on the number of pulses per second per units of measure (litres/minute in
    // this case) coming from the sensor.
    sensors.flow_rate = ((1000.0 / (millis() - previousFlowMillis)) * pulse1Sec) / settings.flow_calibration;
    previousFlowMillis = millis();

    // Divide the flow rate in litres/minute by 60 to determine how many litres have
    // passed through the sensor in this 1 second interval, then multiply by 1000 to
    // convert to millilitres.
    sensors.flowMilliLiters = (sensors.flow_rate / 60) * 1000;

    // Add the millilitres passed in this second to the cumulative total
    sensors.totalMilliLiters += sensors.flowMilliLiters;

    // Print the flow rate for this second in litres / minute
    //Serial.print("Flow rate: ");
    //Serial.print(int(sensors.flow_rate));  // Print the integer part of the variable
    //Serial.print("L/min");
    //Serial.print("\t");       // Print tab space

    // Print the cumulative total of litres flowed since starting
    //Serial.print("Output Liquid Quantity: ");
    //Serial.print(totalMilliLitres);
    //Serial.print("mL / ");
    //Serial.print(totalMilliLitres / 1000);
    //Serial.println("L");
  }
}

void storeTotalMilliLiters() {
  preferences.begin("garden", false);
  preferences.putULong("totalMilliLiters", sensors.totalMilliLiters);
  preferences.end();
}


void readSensors() {
  D_PRINTLN("  [readSensors] Reading Sensors");
  
  state.water = getWaterState();
  
  sensors.dallasValueTemp = getTempValue(temp_sensor);

  sensors.dhtValueTemp = getDhtValueTemp(dht);
  sensors.dhtValueHumidity = getDhtValueHumidity(dht);

  ph.setTemperature(sensors.dallasValueTemp);
  sensors.ph_value = ph.readPH();
  sensors.ph_analog = ph.getVoltage();
  settings.ph_acidVoltage = ph.getAcidVoltage();
  settings.ph_neutralVoltage = ph.getNeutralVoltage();

  tds.setTemperature(sensors.dallasValueTemp);
  tds.update();
  sensors.tds_value = tds.getTdsValue();
  sensors.tds_analog = tds.getAnalogValue();
}

bool trigger(){
  currentMillis = millis();
  if (currentMillis - previousMillis > sensors.interval) {
    D_PRINTLN("triggered");
    previousMillis = millis();
    return true;    
  } else {
    return false;
  }
}

//////////////////////////////////////////////
/// Main part
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
void loop() {
  ws.cleanupClients();
  if (settings.scheduler_active == 1) {
    ts.execute();
  }

  ArduinoOTA.handle();

  if(trigger()) {
    message.timeStamp = updateTime();
    message.dayStamp = updateDate();
    getFlowRate();
    setPumpState();
    setValveState();
    setFanState();
    setLightState();
    readSensors();
    storeTotalMilliLiters();
    notifyClients();
  }
}

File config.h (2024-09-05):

//#define DEBUG

#ifdef DEBUG
#define D_PRINT(x) Serial.print(x)
#define D_PRINTDEC(x) Serial.print(x, DEC)
#define D_PRINTLN(x) Serial.println(x)
#else
#define D_PRINT(x)
#define D_PRINTDEC(x)
#define D_PRINTLN(x)
#endif

#ifndef CONFIG
#define CONFIG

// Pump module pins
#define PUMP1_PIN 27
#define PUMP2_PIN 14
#define VALVE1_PIN 12
#define VALVE2_PIN 15
#define FLOW_PIN 32
// Fan/light module pins
#define FAN1_PIN 16
#define FAN2_PIN 17
#define FANPWM1_PIN 25
// Light rf switch pin
#define RF_PIN 13
// Sensor pins
#define TEMP_PIN 33
#define DHT_PIN 26
#define TDS_PIN 35
#define PH_PIN 36     //A0, VP
#define LEVEL_PIN 39  //A3. VN

// Board voltage and samplerate
#define AREF 3300
#define ADCRANGE 4096.0

// dht type
#define DHTTYPE DHT22

// Default PWM properties
#define PWM_FREQ 25000
#define PWM_FANCHANNEL 0
#define PWM_RESOLUTION 8

// Sensor read interval in ms
#define SENSOR_INTERVAL 1000

// Spray schedule defaults (milliseconds)
#define SPRAY_PERIOD 10000
#define SPRAY_DURATION 1000
#define VALVE1_DELAY 100
// Light schedule defaults (hours)
#define LIGHT_ON 12
#define LIGHT_OFF 12

// Default active pump (1/2)
#define ACTIVE_PUMP 1
// Default scheduler active
#define SCHEDULER_ACTIVE 0
// Default pwm fan speed (0-100)
#define FAN1_SPEED 0
// Calibration defaults
//#define PH_CALIBRATED false
#define PH_NEUTRALVOLTAGE 1500.0
#define PH_ACIDVOLTAGE 2032.44
//#define TDS_CALIBRATED false
#define TDS_KVALUE 1.0
// PH sample size
#define PH_SAMPLESIZE 10
// PH ranges
#define PH_SENSOR_DUPONT
//#define PH_SENSOR_GRAVITY_V2

#ifdef PH_SENSOR_DUPONT
#define PH_8_VOLTAGE 1500
#define PH_6_VOLTAGE 1800
#define PH_5_VOLTAGE 2000
#define PH_3_VOLTAGE 2310
#endif

#ifdef PH_SENSOR_GRAVITY_V2
#define PH_8_VOLTAGE 1122
#define PH_6_VOLTAGE 1478
#define PH_5_VOLTAGE 1654
#define PH_3_VOLTAGE 2010
#endif

// flow ensor
#define FLOW_CALIBRATION 4.5


#endif

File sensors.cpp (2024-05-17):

#include "sensors.h"

// DHT Temperature
float getDhtValueTemp(DHT& dht) {
  float dhtValueTemp = dht.readTemperature();
  if (isnan(dhtValueTemp)) {
    Serial.println(F("Failed to read from DHT sensor!"));
    return -1;
  } else {
    D_SENSOR_PRINT("  [getDhtValueTemp] DHT Temperature:");
    D_SENSOR_PRINTLN(dhtValueTemp);
    return dhtValueTemp;
  }
}

// DHT Humidity
float getDhtValueHumidity(DHT& dht) {
  float dhtValueHumidity = dht.readHumidity();
  if (isnan(dhtValueHumidity)) {
    Serial.println(F("Failed to read from DHT sensor!"));
    return -1;
  } else {
    D_SENSOR_PRINT("  [getDhtValueHumidity] DHT Humidity:");
    D_SENSOR_PRINTLN(dhtValueHumidity);
    return dhtValueHumidity;
  }
}

// 18B20 Temperature
float getTempValue(DallasTemperature& temp_sensor) {
  temp_sensor.requestTemperatures();
  float dallasValueTemp = temp_sensor.getTempCByIndex(0);
  if (isnan(dallasValueTemp)) {
    Serial.println(F("Failed to read from 18B20 sensor!"));
    return -1;
  } else {
    D_SENSOR_PRINT("  [getTempValue] 18B20 Temperature:");
    D_SENSOR_PRINTLN(dallasValueTemp);
    return dallasValueTemp;
  }
}

// water level
bool getWaterState() {
  bool state_water = digitalRead(LEVEL_PIN);
  if (state_water == LOW) {
    D_SENSOR_PRINTLN("  [getWaterState] Water ok");
    return 1;
  } else {
    D_SENSOR_PRINTLN("  [getWaterState] Water low");
    return 0;
  }
}

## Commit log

2023-07-23 Initial commit - pumps, valves and flow meter works via ws
2023-07-23 Add light and fan on/off functionality to to arduino code
2023-07-24 Fix typo, add some debug info and make fans and light switch work
    [ESPonics.ino]
2023-08-19 Set light to seconds for testing and fix pwm control for fan
    [ESPonics.ino]
2023-08-19 Add openscad case models and stl files
    [module_fan_light-bottom.stl, module_fan_light-top.stl, module_fan_light.scad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]
2023-08-19 Add fan adapter openscad model and stl file
    [fan_adapter-110mm.stl, fan_adapter-cover.stl, fan_adapter.scad]
2023-08-19 Add filter openscad model and stl files
    [filter-bottom.stl, filter-top.stl, filter.scad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]
2023-08-19 Add clip bar and clip openscad model and stl files
    [clip_bar-bar_150mm.stl, clip_bar-bar_180mm.stl, clip_bar-bar_77mm.stl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]
2023-08-20 Add first kicad files
    [ESPonics.kicad_pcb, ESPonics.kicad_sch]
2023-08-20 Add bom template
    [bom.ods]
2023-08-20 Add Sensor GPIO definitions
2023-08-20 Add GPIO connections to kicad
    [ESPonics.kicad_sch]
2023-08-20 Add main controller case
    [main_controller-bottom.stl, main_controller-top.stl, main_controller.scad]
2023-08-22 Fix the ethernet port fix
    [main_controller-bottom.stl, main_controller-top.stl, main_controller.scad]
2023-08-22 Add temperature reading code
2023-08-22 Add water state sensor reading code
2023-08-23 Add pull up resistors
    [ESPonics.kicad_sch]
2023-08-24 Enlarge usb access opening in main case
    [main_controller-bottom.stl, main_controller-top.stl, main_controller.scad]
2023-08-24 Add calibration subpage
2023-08-24 Add calibration subpage to code
2023-08-24 Start creating first pcb
    [ESPonics.kicad_pcb, ESPonics.kicad_sch]
2023-08-26 Small pcb changes
    [ESPonics.kicad_sch]
2023-08-26 Add stl files for 80mm fan adapter and small fixes for openscad model
    [fan_adapter-80mm_100mm.stl, fan_adapter-cover-80mm_100mm.stl, fan_adapter.scad]
2023-08-27 Add debug print for easier handling
2023-08-27 Update schematic with new GPIOs
    [ESPonics.kicad_sch]
2023-08-27 Add DHT sensor values to ui
2023-08-27 Add remaining sensor data display to ui and mock ph and ec functions
2023-08-31 Fix water level code and change connected pins.
    [ESPonics.ino, vars.h]
2023-09-03 Add first calibration code
2023-09-03 Use A0 (G39) for ph sensor
2023-09-03 Remove separate calibration page and finish up ph calibration
2023-09-04 Fix seom ph calibration issues
    [ESPonics.ino]
2023-09-04 Adjust pin assignments
2023-09-04 Another pin fix
2023-09-08 Update kicad file
    [ESPonics.kicad_sch]
2023-10-03 Add small connector for alu profile bars
    [bar_connector.scad, bar_connector.stl]
2024-04-23 Add wip bom and overview to docs
    [bom.ods]
2024-05-06 Add delay between turning on pump and opening valve
2024-05-07 Remove OTA as it does not work
    [ESPonics.ino]
2024-05-07 Move pin setup to external function
2024-05-09 Create class for ph sensor
2024-05-12 Add TDS calibration method
2024-05-12 Save calibration parameters
2024-05-12 Move sensor read functions to own file and clean up some more
2024-05-13 Add schematics for fans and light extension
    [ESPonics_module-fans_light.kicad_pcb, ESPonics_module-fans_light.kicad_sch]
2024-05-14 Add kicad schema for sensors module
    [ESPonics_module-sensors.kicad_pcb, ESPonics_module-sensors.kicad_sch]
2024-05-15 Add pump and valve module schematics
    [ESPonics_module-pumps.kicad_pcb, ESPonics_module-pumps.kicad_sch]
2024-05-15 Add kicad backup folders to gitignore
2024-05-15 Add power converter to pump module schematic
    [ESPonics_module-pumps.kicad_sch]
2024-05-17 Read sensors without passing by reference
2024-05-17 Small changes to schematics
    [ESPonics_module-pumps.kicad_sch]
2024-05-23 Add calibration values to ui and temp compensation for tds
2024-05-23 Add flow variables to structs
2024-08-25 Change ph calibration to detect value and prepare for logging
2024-08-26 Clean up calibration frontend and add log messages to calibration
2024-08-31 Fix date and time retrieval
    [ESPonics.ino, vars.h]
2024-08-31 Adjust timezone and small fix
    [ESPonics.ino, vars.h]
2024-09-04 Create helper file and put setup functions there, fix small issues
    [ESPonics.ino, helper.cpp, vars.h]
2024-09-05 Clean up flow sensor count and store totalflow regulary
2024-10-31 Add Flow calibration functionality
